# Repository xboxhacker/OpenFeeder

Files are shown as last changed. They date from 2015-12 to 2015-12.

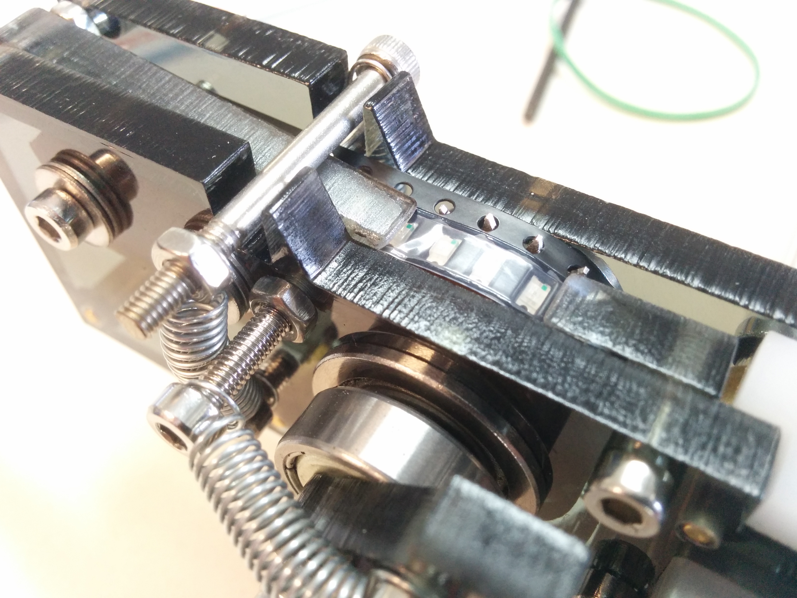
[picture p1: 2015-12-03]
PHOTOS/IMG_20151105_131929.jpg

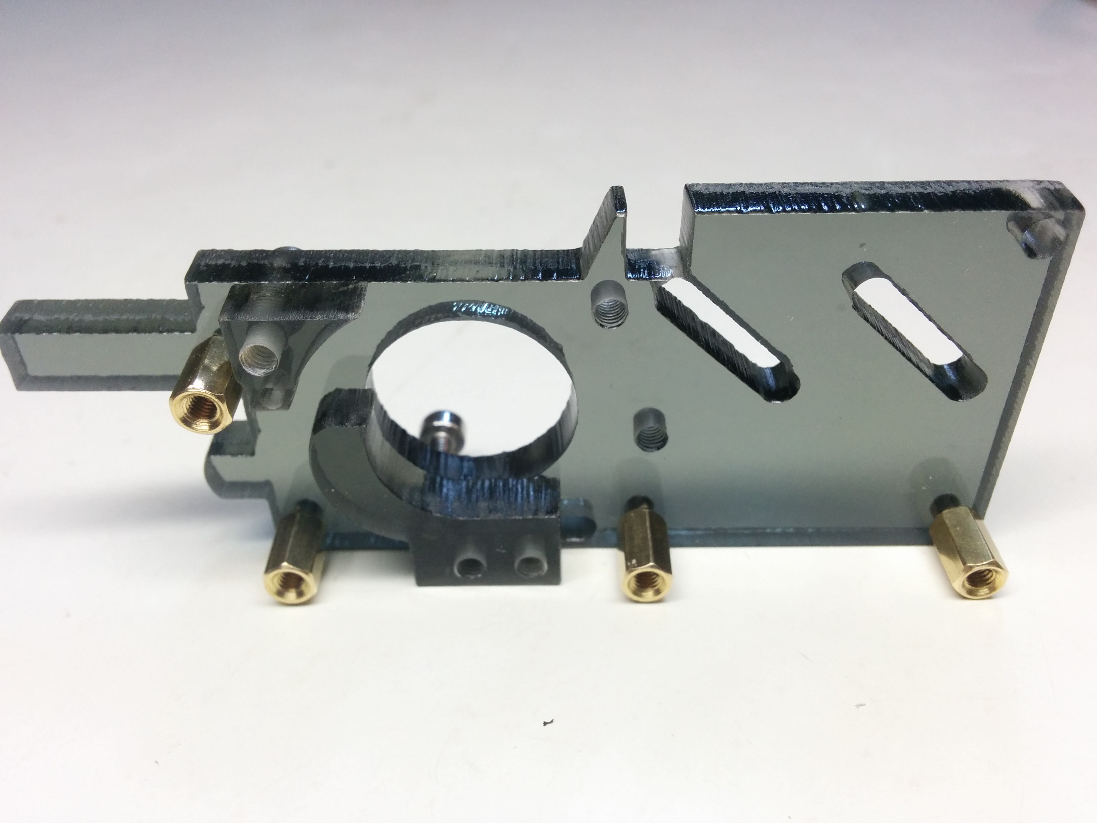
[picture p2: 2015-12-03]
PHOTOS/IMG_20151103_192846.jpg

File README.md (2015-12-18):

# OpenFeeder
OpenSource mechanical feeder design for DIY and OpenPNP community!

This feeder design is for MY machine. Extensive modifications to existing machines may be necessary to accommodate it. Its meant to fit a 20mm aluminum t-slot. I am using t-slots from MakerSlide. 

Feel free to edit the source file. You must post edited files for all the use.

OpenFeeder discussion can be found in the [OpenPNP google group](https://groups.google.com/forum/#!forum/openpnp).

OpenFeeder was made with SketchUp 2013. Each part is on its own labeled layer.

Current source version: OpenFeederRev7.skp

# OVERVIEW:

Key Features:
* Simply made form .250″ acrylic sheet on a laser cutter (3d printable too).
* Easily accessed and cheap components for the drive system.
* Easily changed over to different size tapes, 8mm 10mm 12mm etc.
* Adjustable tape height, from paper resistor tape to tape with electrolytic caps.
* Designed to work with 20mm T-slot.
* “Almost” infinite feeding distance. Able to feed tape form .05mm at a time to 12mm at a time.
* Very smooth feeding, even at a very high speed.
* Most likely over engineered!

Basic Operation: 
* tapeAdvanceArm is pressed down, tape is advanced. The more the arm is pressed, the more the tape is advanced (vise versa).
* Tape plastic cover is pulled backward with a small fishing weight.

Advanced Operation: 
* Both the tapeGuide and the exitGuide are adjustable for paper tapes heights and embossed tapes heights. See examples in photos folder.
* Wider tapes can be used by changing the tapeGuide width and the 8mm brass standoff height.
* As tapeAdvanceArm is pressed, the one way bearing is locked in rotation, thus turning the tapeSprocket. Once the tapeAdvanceArm is released, the one way bearing un-locks and allows the arm to return to the ready position. 

# File List:

* openfeederRev7.skp - Sketchup file of the entire feeder
* tapeSprocket_FULL.skp  - Drive sprocket w/ back spacer
* tapeSprocket_Backer.skp  - Sprocket back spacer ONLY
* tapeGuide.stl  - 3D printable tapeGuide part

# BOM:

**Laser Cut Parts:**
* bodyLeft
* bodyRight
* exitGuide (two parts)
* tapePresser
* tapeAdvanceArm
* washer

(These parts can be 3D printed)

**3D Printed Parts:**
* tapeGuide

(This part can be CNC milled)

**Other Parts**
* tapeSprocket

(This part is tricky… should be cut from stainless steel. But can be 3D printed)

**Hardware Parts:**
* 626Z-FB (Flange Bearing 6x6x19) - 2pcs
* EWC0608 (Hex One Way Bearing 6x8x10)  - 1pcs
* 8mm Tall Brass Standoff (M3 Thread) - 3pcs
* M3 x 8mm Cap Screw - 7pcs
* M3 x 16mm Cap Screw - 2pcs
* M3 x 20mm Cap Screw - 1pcs
* M6 x 30mm Cap Screw - 1pcs
* M3 Nuts  -  2pcs
* M6 Nuts  -  1pcs
* M6 Washers  -  2-6pcs
* Small Extension Springs or Rubber Bands
* M5 t-slot nut

**Tools:**

* M3 Tap 

* Metric Allen Key Set

* Grinder

# Assembly:

Threading:
* Check photos folder for thread_chart.jpg for threading info.
* Lubrication is needed to thread acrylic. Simply use a drop of dish soap in some water. DO NOT USE PETROLEUM BASED LUBE!! It will end up cracking the acrylic.

More soon.... check the photos for more info.

# WARNING:

This is my very first ever 3D Cad design. So these might be some errors in the source. I am to be held harmless for any problems any errors or omissions may cause. All sources are provided "AS-IS", and without warranty.

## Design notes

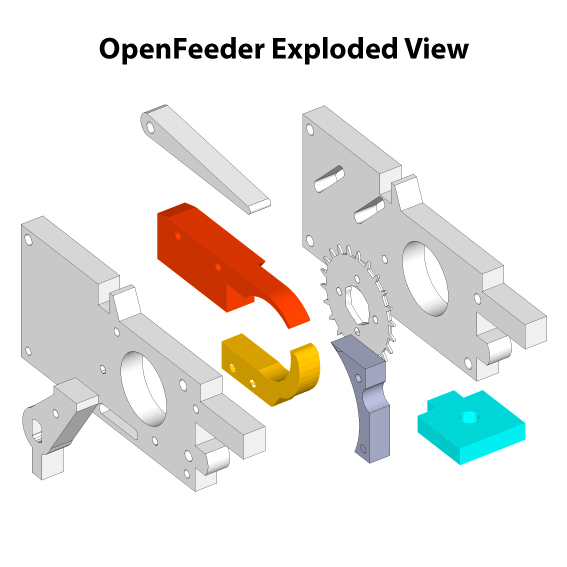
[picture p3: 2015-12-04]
PHOTOS/exploded_view.jpg

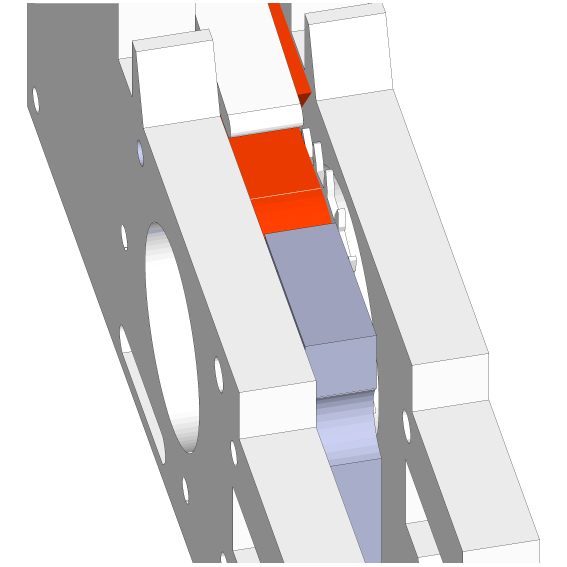
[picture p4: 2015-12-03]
PHOTOS/view1.jpg

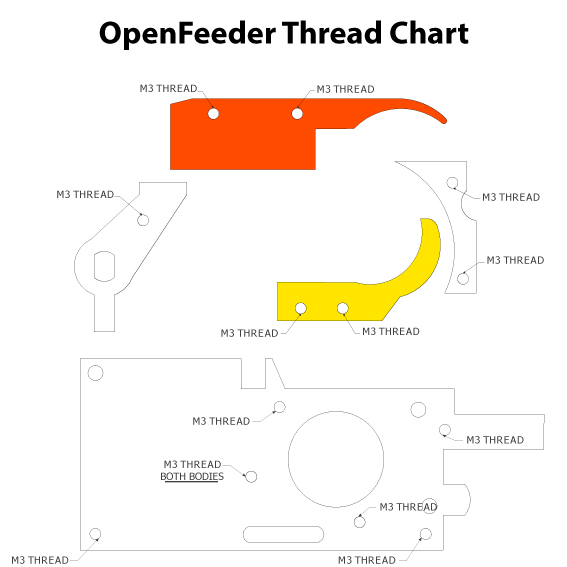
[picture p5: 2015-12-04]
PHOTOS/thread_chart.jpg

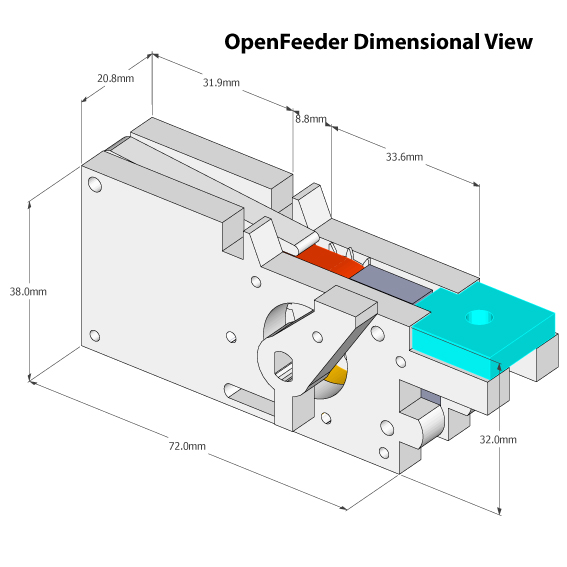
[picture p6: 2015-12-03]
PHOTOS/dimension_view.jpg

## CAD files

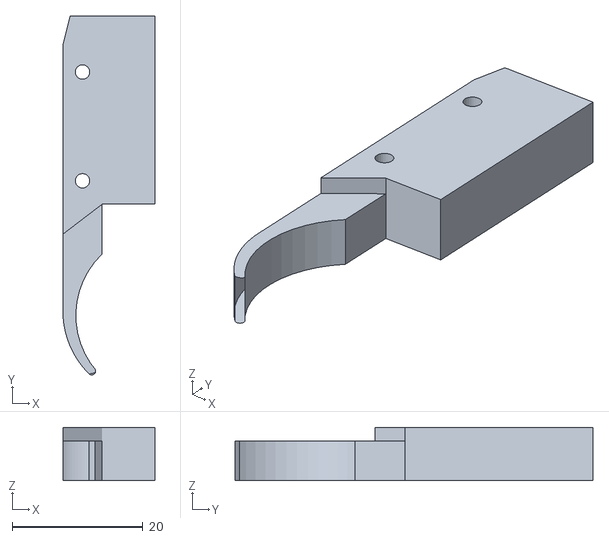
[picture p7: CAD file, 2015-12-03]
tapeGuide.stl
14.1 x 54.9 x 8.10

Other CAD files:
openfeederRev7.skp
tapeSprocket_Backer.skp
tapeSprocket_FULL.skp
